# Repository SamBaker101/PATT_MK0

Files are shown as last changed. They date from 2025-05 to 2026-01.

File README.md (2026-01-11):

# PRINT ALL THE THINGS!

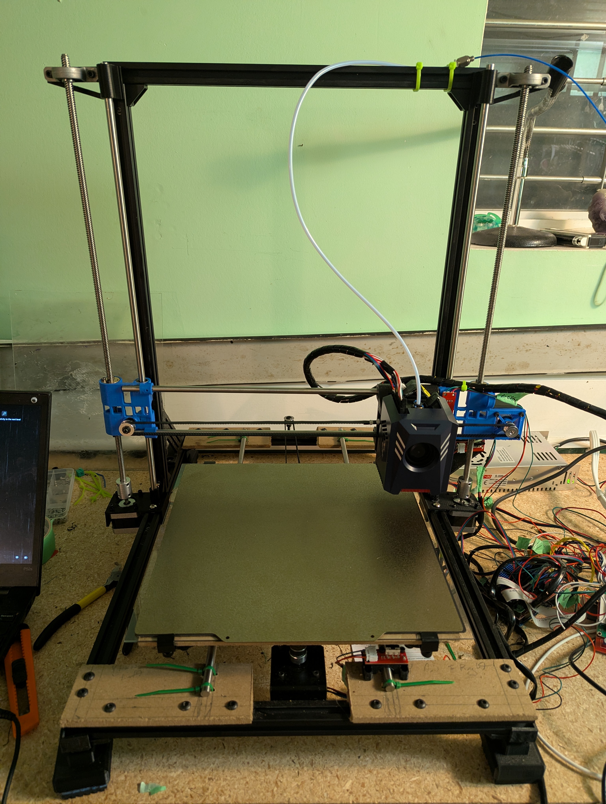
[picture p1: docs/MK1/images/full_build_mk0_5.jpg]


## Overview

A Cartesian, Bed-slinger style, printer. Y motion is applied to the print plate while the hot-end moves in the X and Z directions. This design was selected to give a simple starting point to begin 3d printing. At this point the printer is still a prototype though it does now complete prints reliably. I am working to make incremental improvements to the design over time. More details about my longterm plans can be found in the roadmap below.

- AnyCubic Kobra 2 Direct Drive Extruder Assembly
- Print Area:  290 x 180 x 300 mm (Y will be 250-290 after redesign) 
- Total Size:  480 x 540 x 540 mm
- Arduino Mega - Marlin Firmware
- Reprap 1.4 Control Board
- Orange Pi 4 LTS (Octoprint server)

## Roadmap

The following milestones will be used to direct my efforts in this project. My overall philosophy here has been to begin with the simplest and lowest cost printer possible, regardless of its print speed and quality. Now that the basic device is built I have begun iterating on it to improve its function and reliability.

### MK0 - Zip Ties and Prayers ---- Done!

- Goal: Print a cube
- Status: Complete
- Expected Date: 06/30/2025 
- Completion Date: 07/14/2025
- Comments:  This is meant to be a minimum viable product. The only expectation is that I can connect to it, upload g-code and the printer will make a recognizable attempt to print it. At this time I will not be concerned with the print speed or any issues with the output (within reason). It is also notable that for this step I will not have access to 3d printed parts so many of the brackets and connections will need to be made with a combination of particle board, zip ties and assorted hardware.  
 - [Debrief](https://github.com/SamBaker101/PATT_MK0/blob/main/docs/MK0/MK0_debrief.md)  
 - [Testing](https://github.com/SamBaker101/PATT_MK0/blob/main/docs/MK0/MK0_testing.md)  
 - [BOM](https://github.com/SamBaker101/PATT_MK0/blob/main/docs/MK0/MK0_BOM.csv)     

### MK1 - It Prints Itself?

- Goals: 
     - Replace all temporary parts with self printed parts, these parts must be reliable, consistant and free of major artifacts. 
     - Reorganize electronics onto a board or container integrated into the printer body.
     - Add capability to print remotly over wifi.   
- Status: In Progress
- Expected Date: -
- Comments: Once MK0 is able to complete prints I will begin replacing the temporary plywood parts with custom designed 3d printed parts. I expect this to be an iterative process as replacing selected parts should increase the overall print quality which would in turn allow me to make better versions of those parts. At this time I will also be adding mechanical belt tensioning systems and a reliable bed leveling mechanism. I will also create an electronics board beneath the print bed and clean up the wire routing. Having my laptop wired to print is a major pain point so I will also be adding an OctoPrint server to manage prints.
 - [Debrief](https://github.com/SamBaker101/PATT_MK0/blob/main/docs/MK1/MK1_debrief.md)  
 - [BOM](https://github.com/SamBaker101/PATT_MK0/blob/main/docs/MK1/MK1_BOM.csv)     

## MK2 - Use It

- Goal: 
     - Print a Benchy in under 45min with no major quality issues
- Status: Planned
- Expected Date: Open
- Comments: I think it's important here to use the printer for it's intended purpose for few weeks-months building other projects. I am eager to begin work on some new robotics projetcs and to explore the organizational print community so this shouldn't be a struggle. This will give me a better sense of the printers capabilities and it's pain points.  As I become more familiar with the printer I will iterate on the custom parts and look at other enhancements that can be made to improve performance. 

### MK3 - Upgrade$$$

- Goal: 
     - Print Benchy without major errors in PETG, TPE and ABS. 
     - Print in place chainmail in PLA.
     - Print Benchy in PLA in less than 30 min
- Status: Planned
- Expected Date: Start date + 2 months
- Comments: In my initial build I generally went with the lowest cost option to avoid any expensive mistakes, Now is the time to correct that. Upgrade the control board, motor controllers and hot end to competitive versions. At this time I will also add a heated bed and upgrade any of the PLA printed parts as required. By now I can expect to be well aware of any other issues in the build (linear rods, lead screws ect), so I will take care of any of these issues which I've been putting off.

#### MKZ - Next Steps
- Explore alternate configurations (Core XY, Delta 3d ect.)
- Build a vented, temperature controlled (and sound insulating) cabinet
- Add a second extruder
- Build an AMS
- Build a dry box

## Electrical

| Part | Part Detail | Number | Voltage |Current | Power | Comment |
|---|---|---|---|---|---|---|
|Stepper |Nema 17 | 5 |  24V |1.7A | 40.8W | |
|Motor Controllers |TMC2209 | 4 |  24V |7.5mA | 180mW | Z-Axis can share controller, RAMPS board may need modification to use these  |
|Hot End |Anycubic Kobra2| 1 |24/5V|| 60W | This is temporary but will get me up and running, Power number is a rough estimate as hard numbers are limited  |
|Driver Board |RAMPS1.4 | 1 |  24V || | Interested in designing my own in future, Needed slight modification to run at 24V|
|Main Board |Arduino Mega | 1 |  5V || | Draw 5V off RAMPS board, cut power diode on RAMPS to avoid running 24V in| 
|Limit Switches |Leaf Switches  | 3 | || | |
|Heated Bed |? | 1 | || | Will leave off initial build and upgrade later |
|PSU |LEDMO | 1 | 24V | 20A | 480W | https://www.amazon.ca/gp/product/B08975B78Z/ref=ox_sc_act_title_4?smid=A38O99J0OT8HQ0&th=1  |
|Fans | | 1+ | 12-24V || | |  
|OctoPrint Server |Orange Pi 4 LTS| 1 | 5V || | Has been a bit unreliable so I may switch to an RPi Zero 2W|

### Electronics Box

As part of the MK1 improvements to the original prototype I am currently designing a small sidecar which will house the Arduino Mega (With RAMPS board), The Orange Pi (Being used for Octoprint) and the Reprap Display Board. I am using a sidecar design as the Y-axis design is not yet finalized. In future I may move these electronics under the print bed/y-axis to minimize the printer's footprint.

In order to simplify the wiring I will be organizing the outputs on the back of this box into two D-Sub 25 pin connectors. One of these connectors will have the 18 pin connections for the hotend as well as the 4 pins used to drive the extruder motor. The other contain the other 16 motor connections and the 9 endstop wires. By combining some of the ground and VDD connections I should also be able to allow space for a printed bed in future. I will mismatch these connectors (Male for the printhead and female for the motors) to avoid the possibility of them being plugged in backwards.

The box will also have power inputs for the Orange Pi (USB-C) and the RAMPs board (24V from PSU).

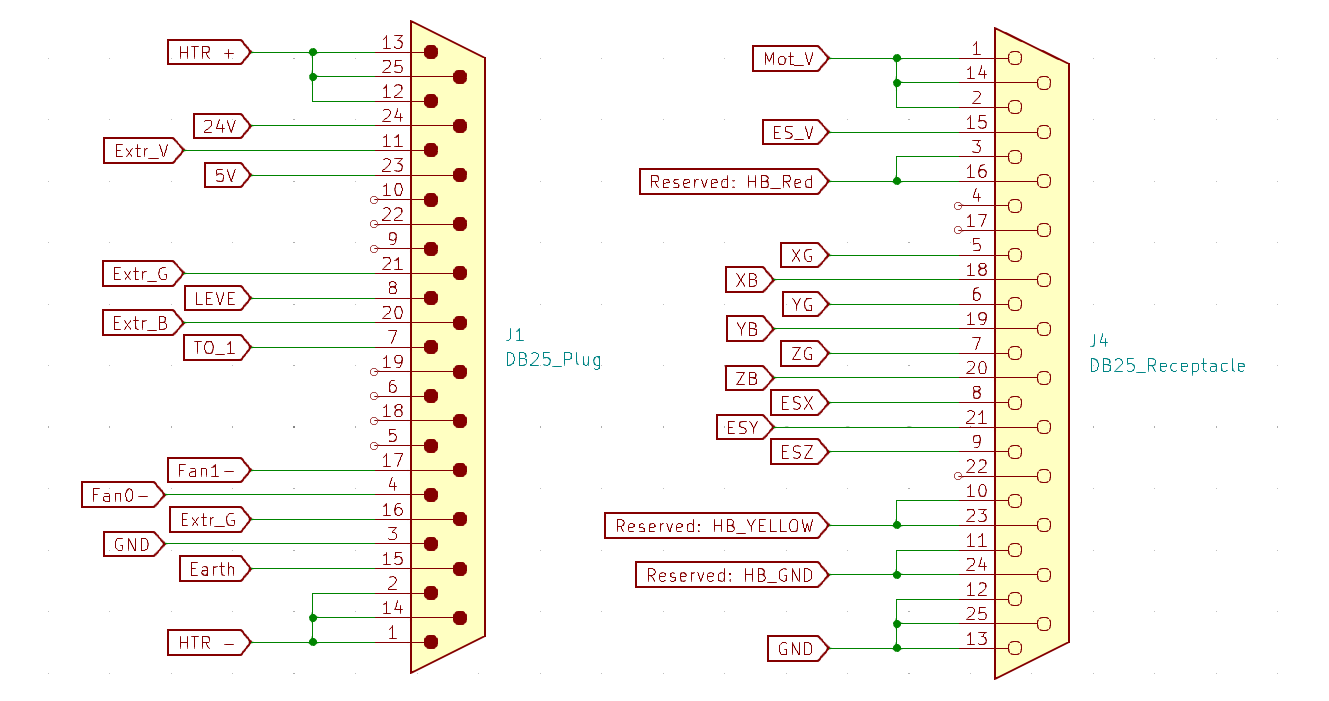
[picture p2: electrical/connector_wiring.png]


## Modelling

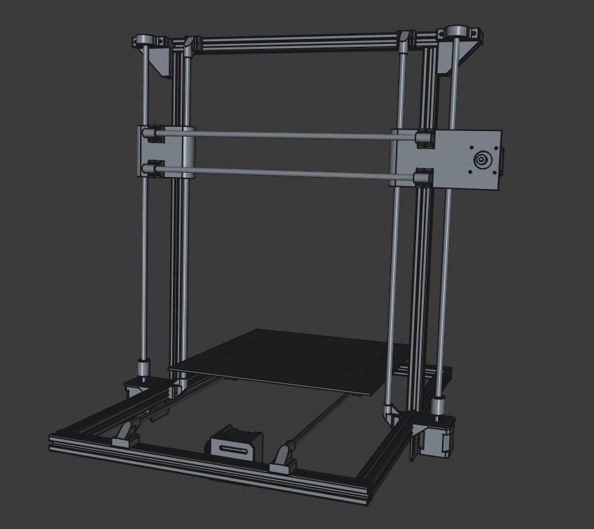
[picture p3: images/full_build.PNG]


NOTE: These models are approximate versions created while developing the printer design. I am in the process of redesigning a number of the parts and will be updating these assemblies as I solidify their new models.

The model is broken into 3 primary sections, one for each axis. The Y-axis assembly includes the print plate while the X-axis includes the hotend and extruder. Each of these main assemblies is further divided into sub assemblies to isolate different segments such as motor drives, frame segments, ect. 

All models were created using FreeCAD 1.0. FreeCAD can be downloaded at the following link.

https://www.freecad.org/

### Models

#### Full Frame

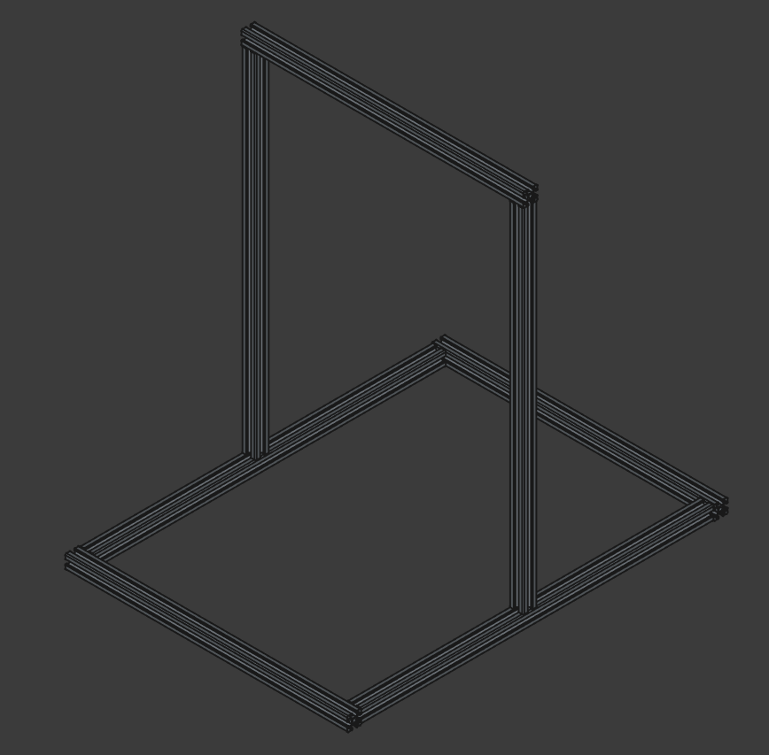
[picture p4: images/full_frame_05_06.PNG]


#### Y-Axis

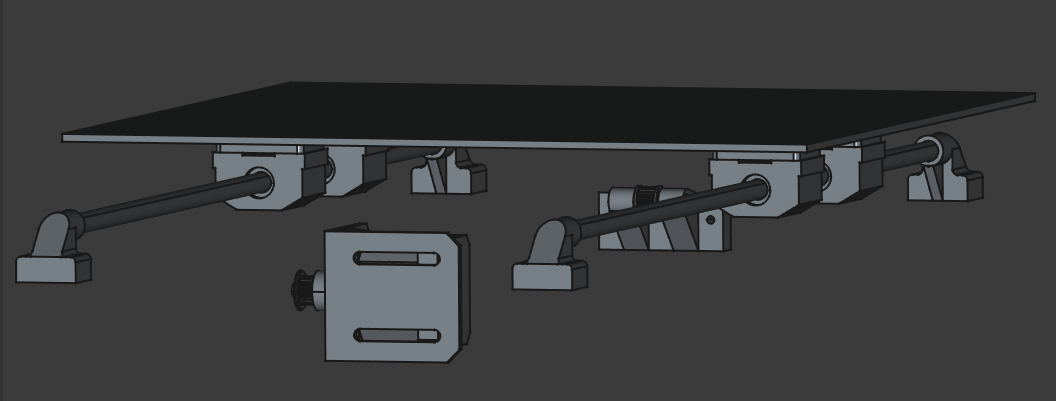
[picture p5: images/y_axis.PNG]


#### X-Axis

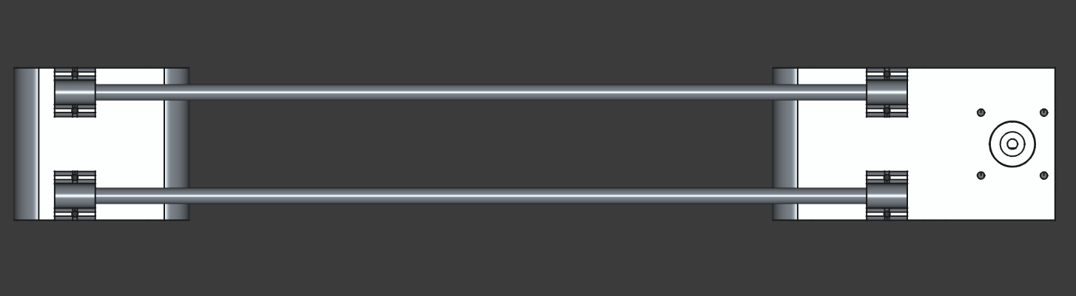
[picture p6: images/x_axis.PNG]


#### Z-Axis

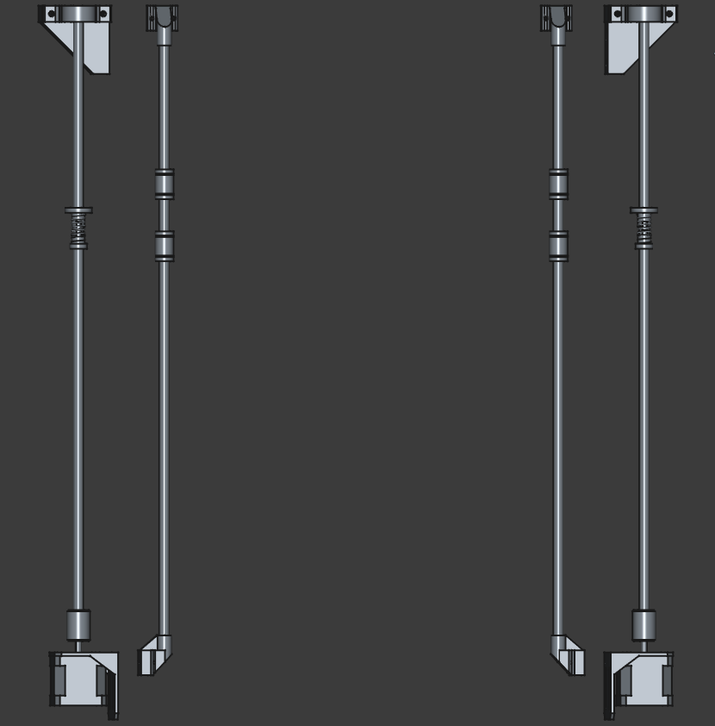
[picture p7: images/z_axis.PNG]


## Parts

My initial approach to part selection was to minimize cost wherever reasonable. My goal was to build a functional printer without a strong focus on print speed or quality. This was to allow time to develop my own skills and identify any knowledge gaps or incorrect assumptions I have.  

Now that I have created a prototype device, I will begin iterating on the device and replacing those lower cost parts with higher end equipment to improve overall quality.

[MK0 BOM](https://github.com/SamBaker101/PATT_MK0/blob/main/docs/MK0/MK0_BOM.csv)

### Custom Parts

Now that MK0 is complete I am beginning the process of replacing the wood panel parts with 3d printed ones. Additionally there are a number of fairly hackey fixes (tensioners, bed leveling, endstops ect) which need more robust solutions.

As I design these new parts I will place the stl files [here](https://github.com/SamBaker101/PATT_MK0/tree/main/models/custom_parts).

Additionally I will include pictures and short descriptions of each part in this [document](https://github.com/SamBaker101/PATT_MK0/blob/main/models/custom_parts/custom_parts.md).

As I get into replacing the more structural components of the build I will also replace the draft assemblies with new more accurate ones.

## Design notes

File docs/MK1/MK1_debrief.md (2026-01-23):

# MK1 - Basic Prototype

Note: MK1 is still in progress. At this point I've redesigned the X and Z axis though further refinement is still necessary.

## Background

The primary goal of MK1 is to move from the somewhat hacked together MK0 to a more robust and coherent platform that I can build on for future developements. This primarily involves replacing the wood panel parts with 3d printed ones. The majority of the zip ties should also be removed during this step. In adition I have added an Orange Pi to run an OctoPrint server. Finally I will be making some refinements to the wiring and electrical system. 

## Build Overview

### New Part Designs
### Octoprint Server

## Configurations

## Lessons

## Next Steps

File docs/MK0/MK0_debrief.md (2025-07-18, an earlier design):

# MK0 - Basic Prototype

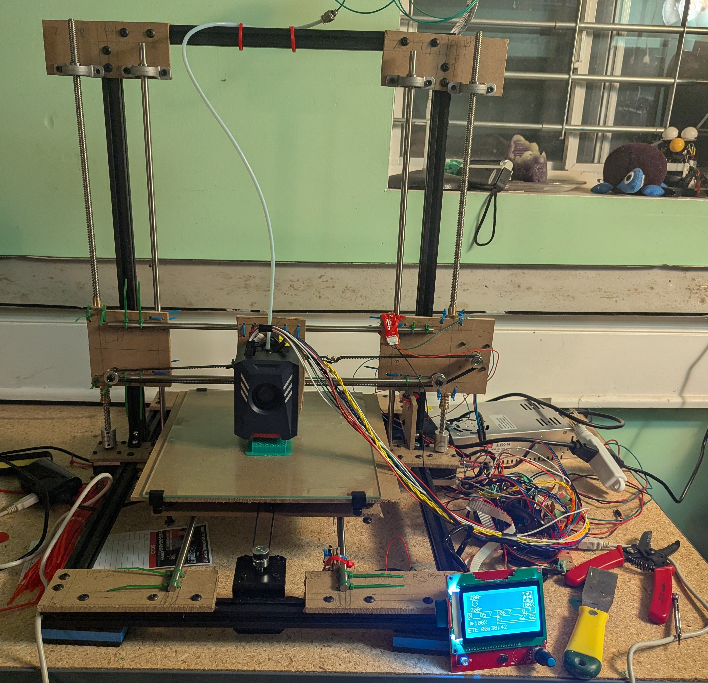
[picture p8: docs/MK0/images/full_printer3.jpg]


## Background

It's not pretty... but it works

The primary constraint with this prototype was one many people run into when building their first 3d printer. That is, that I didn't have a 3d printer. Since I couldn't easily prototype or manufacture custom parts I limitted myself to using only parts I could make using basic tools. These tools included a jig-saw, a power drill, a soldering iron and a variety of hand tools. 

I opted to start with a large build area. My initial plan was to have a full 300mm cubic build space though unfortunately for this initial prototype I ended up having to limit that to 175mm x 175mm x 250mm (more on that later). This may have been for the best as bed leveling proved challenging on this initial build.

While it's my intention to create my own printhead for this project I initially used a direct drive head from an Anycubic Kobra 2. I selected this for it's low cost and the fact that it was complete and self contained. A word of caution is that Anycubic does not open source their hardware or software so I did have to do some reverse engineering to get it working. I will not be publishing the details of that reverse engineering to avoid posting any copywritten IP.

The printer is based on the REPRAP 1.4 control board using an Arduino MEGA board. It operates using Marlin firmware.

## Build Overview

The main frame is built using a combination of aluminum extrusion and composite wood paneling that has been cut to sizes/shape and drilled as required. It is held together with a combination of metric hardware and zip-ties.

As discussed prior I am using an Anycubic printhead which moves in X on a belt driven carriage. The X-axis then moves vertically (Z) on a pair of lead screws.

The bed is a pane of glass which slides in the Y direction (Forward and Back) on a belt drive. This glass pane is supported by 4 bolts which can be adjusted to level the print bed.

Currently the electrical components (REPRAP board and power supply) are stored on the table beside the printer.

## Configurations

Full config details can be found in the Marlin configuration document here:  
[Configuration.h](https://github.com/SamBaker101/PATT_MK0/blob/main/software/Marlin-2.1.2.5/Marlin/Configuration.h)  

All stepper motors are set up to use 1/16 microstepping.

As mentioned above I have restricted the printer to use a 175x175x250mm build space. At time of writing I have not yet tested larger prints but will be doing so shortly.

In my initial testing I had the Z axis bind when using too high of a feedrate. For this reason I have significantly limited the speed of the printer. I have not tested the limits for these metrics as yet but will begin increasing them slowly as I begin building the parts for MK1.  

## Lessons
While perfection was never the goal here this project was not without it's problems. Below I would like to detail some of the main issues I encountered building this prototype and discuss the lessons learned from them. 

### Bed Size and Verticle Rods
As mentioned earlier I had to reduce the bed size from my projected 300mm cubed to 175x175. This was due to the geometry of the x and y axis. 

For the X-axis I opted to have the verticle rods sit inside the frame. This choice was made to simplify the brackets used to hold these rods. Additionally since I was using composite panels I ended up having to make the X carriage and brackets larger than expected which blocks some of the X travel.

The Y-axis has similar issues with the size of it's brackets but also could be corrected by placing the bearings closer together so that the bed could hang over these brackets further. This is a double edged fix though as it could impact the stability of the bed.

This is also the reason I am using a plain glass panel as a print surface. I purchased a removable build plate which I will be using for future iterations but it does not fit on the current build.

### Z-Endstop Relocation
In my initial design I had the Z-Endstop at the top of the axis. When testing I found it was very difficult to get a consisting starting position on prints. To mitigate this I moved the endstop to the bottom.

The major difference here is that when the endstop is at the top you can configure the starting position via software, telling the axis how far to move from it's home position. Now the endstop would need to be physically moved to adjust the height from the build plate. 

This may be less of an issue in future builds where the frame and axis have less slop. In all likelyhood though, I will eventually switch to a bed probe of some kind. That means I am not too concerned about this change going forward. 

### Bed Leveling Issues
My bed leveling mechanism consists of 2 panels. The lower panel holds the bearings and has a bolt in each corner. These four bolts are placed from below facing up with a nut placed loosely on each. tightening or loosening the nut adjusts how much of the bolt stands above the plate while the remainder of the bolt hangs below.

The upper panel holds the glass buildplate. Glued to the bottom of the upper plate are 4 spacers which sit overtop of the bolts.  

This system works but can be frustrating to use for the following reasons. 
- There is quite a bit of slop between the two plates
- 4 Adjustment points are being used when only 3 are required
- Bolt must be held while nut is turned
- Nuts/Bolts can be very hard to reach

I will be redesigning this system to make it simpler and easier to use in future iterations. This will include adding wheels to help turn the nuts (and/or bolts) and adding tension springs below the lower plate to keep the bolts stabalized.

### Wood Panelling is not Nice
Because I am the way I am, I went to the hardware store and bought the cheapest "wood" I could find to create the brackets. This came in the form of a composite panelling which appears to be some kind of compacted cardboard product... 

While functional it is deeply unpleasant to work with. It flakes away in layers when being drilled or cut and produces huge amounts of dust and shavings. if I was doing this again I would definitely spend a few extra dollars for a better material.

Luckily these panels were always meant to be temporary. As I redesign the printer for MK1 I will be removing these parts and replacing them with printed ones.

### Hotend Sag
Because I used a direct drive extruder the hotend is fairly heavy. This combined with the makeshift X carriage causes the printhead to sag. This means the hotend is not perpendicular to the build plate. 

The problem is not significant enough to cause prints to fail but definitely influences the quality. For the next iteration I will be creating a new X carriage and printhead bracket so this issue will be corrected at that point.

## Next Steps

- Replace The Panelling and Zip Ties
- Add Feet and Additional Braces to Frame
- Straighten Belt Runs and Add Tensioners
- Create Room for Full Sized Bed
- Create Better Bed Leveling System
- Remodel Print Head Carriage
- UART for Motor Controllers
- Increase Print Speeds
- Add Electrical Board and Fix Wire Routing

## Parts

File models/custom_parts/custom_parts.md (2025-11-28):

# Custom Parts

## Print Bed
### Bed Leveling Wheel
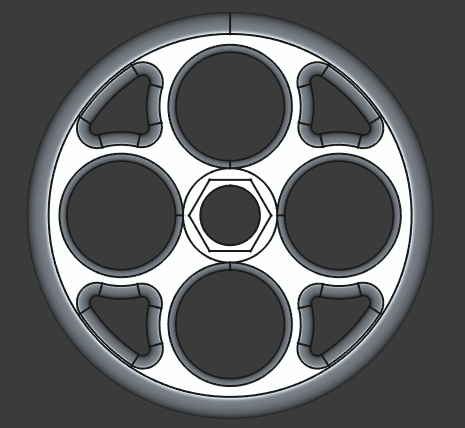
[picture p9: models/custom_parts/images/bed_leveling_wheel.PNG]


Simple wheel to sit over bed levelling nuts and make adjustment easier. This is a quick mock-up which I may return to later to refine.

### Adjustment Bolt Sleeves
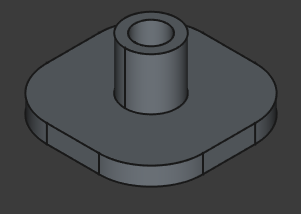
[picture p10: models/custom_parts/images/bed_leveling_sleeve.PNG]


The spacers I used in the initial build have too large an internal diameter so there is slop in the bed, especially if the level screws are set too high. Additionally they are simple cylinders so the glue joints break easily. This part is meant to correct these issues.

### Spool Holder
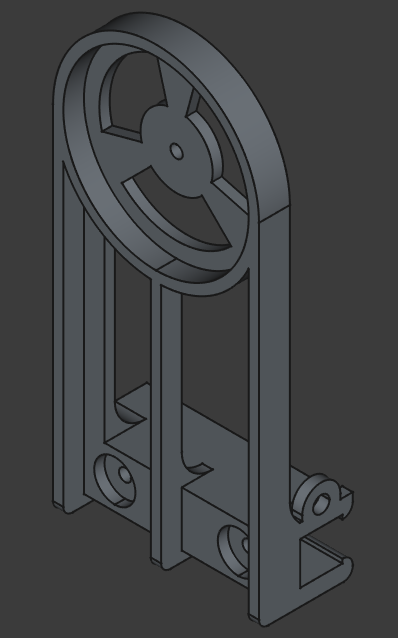
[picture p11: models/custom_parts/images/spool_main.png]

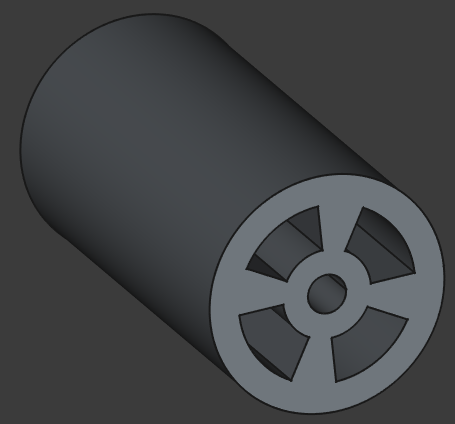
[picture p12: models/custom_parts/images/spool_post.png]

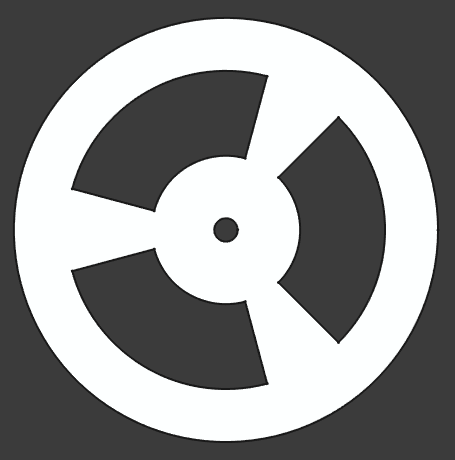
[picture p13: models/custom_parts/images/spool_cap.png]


Spool holder for the top of the printer. I had to go back and add some ribs to strengthen this print. If it is still to week I may try a carriage style design where the post is reenforced on both sides.

### Lower Bed Carrier
### Bed Carrier

## Structural
### Feet
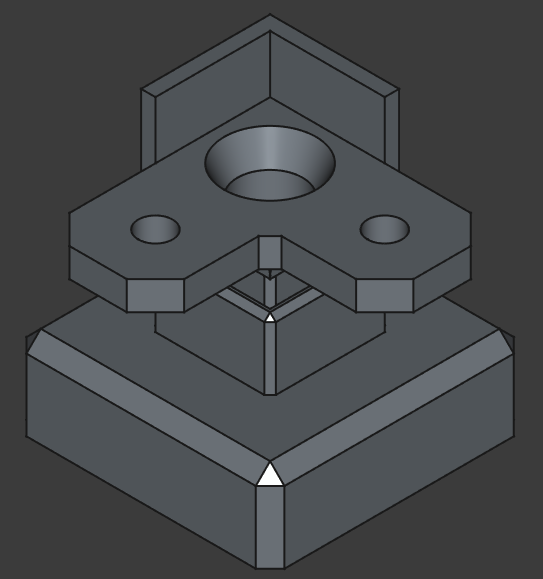
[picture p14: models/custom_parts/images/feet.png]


It's a foot! This is meant to stabalize the frame as well as raise the printer to allow room for the electronics board. Comprised of two seperate pieces (Bracket and Base). Rubber blocks will be attached to the base.

One change that I will make in my next iteration of this part ill be to extend the tabs which bolt to the frame. The screw holes on these tabs currently overlap with the lower portion of the foot making tightening the screws challenging.

### Corner Re-enforcements
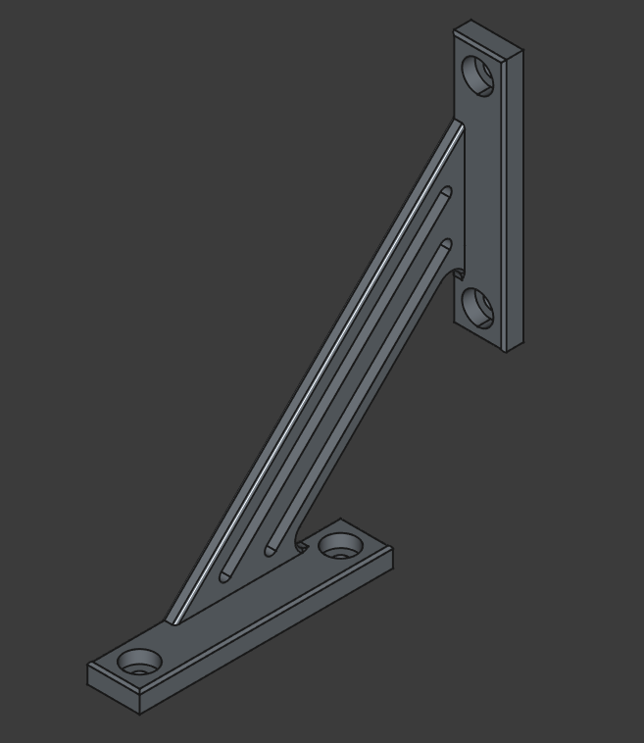
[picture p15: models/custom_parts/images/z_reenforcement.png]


This is a simple bracket to stabalize the connection between the z axis frame and the lower (y-axis) frame.

## Brackets and Carriages
### Y-Axis Brackets (Front and Back)
### Z-Axis Brackets (Top and Bottom)

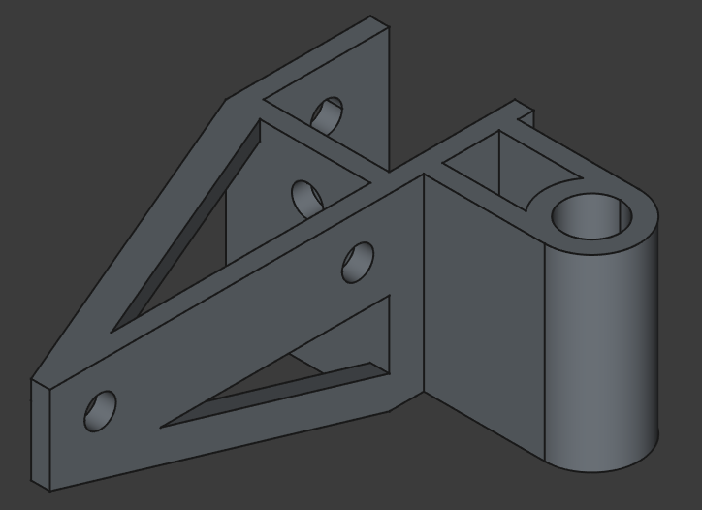
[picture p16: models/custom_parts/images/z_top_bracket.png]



Lower bracket is not strong enough. Also center motor hole is two small. Second revision being tested.

### Z Carriages (Left and Right)




These carriages are working fairly well. They could use some reenforcement though I did print them with limitted infill/resolution so reprinting may help.

End stop holder should be moved up slightly to give clearance for timing belt. More space should be opened between threaded z-rod attachments to simplify installation.

More space is needed for x axis to pass through body, I had to drill/melt to make space.

### X Carriage



Insufficient space for extruder motor so I've had to use a spacer, support flaps interfering with timing belt need to be repositioned (I snapped them off for now).

## Electrical Components
### End Stop Holders


This is a bracket to hold the limit switches. The bracket is designed to allow for minor adjustment of the switch position. This initial version of the bracket is made to work with the current wood panel frame brackets and will need to be revisited as I refine the rest of the frame design. The Z-Axis will require an additional bracket to hold the limit switch out from the frame in the correct position.

### Z Endstop Holder


This holder works in conjunction with the general endstop holder to hold the z limit switch away from the frame. The slots alow fine tuning of the z height.

### Electrical Component Board
### Cable Management Aids

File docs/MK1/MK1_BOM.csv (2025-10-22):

Num | Quantity | Part | Description | Link
0 | 1 | Glass Pane | 12 x 12 | I took this from a thrift store picture frame
1 | 4 | Linear Bearing | Bearing
2 | 2 | Belt Clamp | Part of timing belt kit
3 | 2 | Timing Belt | Part of timing belt kit
4 | 2 | Timing Belt Idler | Part of timing belt kit
5 | 1 | Timing Belt Gear | Part of timing belt kit
6 | 2 | Linear Rod 400mm | 8mm diameter rod
7 | 4 | Linear Rod 500mm | 8mm diameter rod
8 | 3 | 2020 T extusion 400mm | 2020 T extrusion
9 | 4 | 2020 T extusion 500mm | 2020 T extrusion
10 | 10 | 2020 L-Bracket | 2020 Extrusion compliant L-bracket
11 | 4 | Stepper Motor | Nema 17
12 | 1 | Stepper Bracket | L Bracket for Nema 17 stepper motor
13 | 1 | Power Supply | 24V 5A power supply
14 | 1 | Controller | Arduino Mega 2560
15 | 1 | RAMPS1.4 Board | RAMPS1.4 board
16 | 4 | Stepper Motor Driver | TM2209 stepper motor driver
17 | 1 | LCD Display | 12864 LCD display
18 | 1 | DC-DC converter | 24V -> 5V cpnverter for Arduino and LCD
19 | 1 | Safety Plug | Fused wall outlet plug
20 | 3 | Endstop Switch | Mechanical endstop switch
21 | 1 | Hotend Assembly | AnyCubic Kobra2 Direct Feed Hotend Assembly
23 | 1 | Print Surface | 290x290mm PEI print surface
25 | 2 | Lead Screw | 8mm diameter 8mm lead
26 | 2 | Lead Screw Nut | 8mm lead screw nut
27 | 4 | 8mm Lead Screw Bearing | Came with lead screw
28 | 2 | 8mmx5mm Lead Screw Coupler | Coupler for lead screw
29 | 50 | M5 T-Nut | 2020 extrusion compliant T-nut
30 | 18 | M5x8mm Button Head Screw | Standard Metric screw
31 | 30 | M5x12mm Button Head Screw | Standard Metric screw
32 | 2 | M5x16mm Button Head Screw | Standard Metric screw
33 | 4 | M8x35mm Button Head Screw | Standard Metric screw
34 | 4 | M8x22mm Spacer | Plastic spacer for M8 screw
35 | 4 | M8 Hex Nut | Standard Metric nut
36 | 8 | M3x6mm Hex Head Screws | Standard Metric screw
37 | 8 | M4x6mm Hex Head Screws | Standard Metric screw
38 | 1 | PLA | 1KG Spool
39 | 1 | Orange Pi 4 LTS

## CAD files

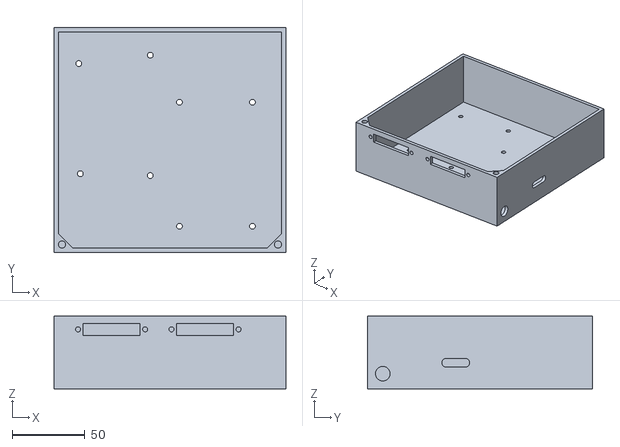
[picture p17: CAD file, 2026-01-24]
models/custom_parts/electrical/electronics_box_main.stl
159.0 x 154.2 x 50.0

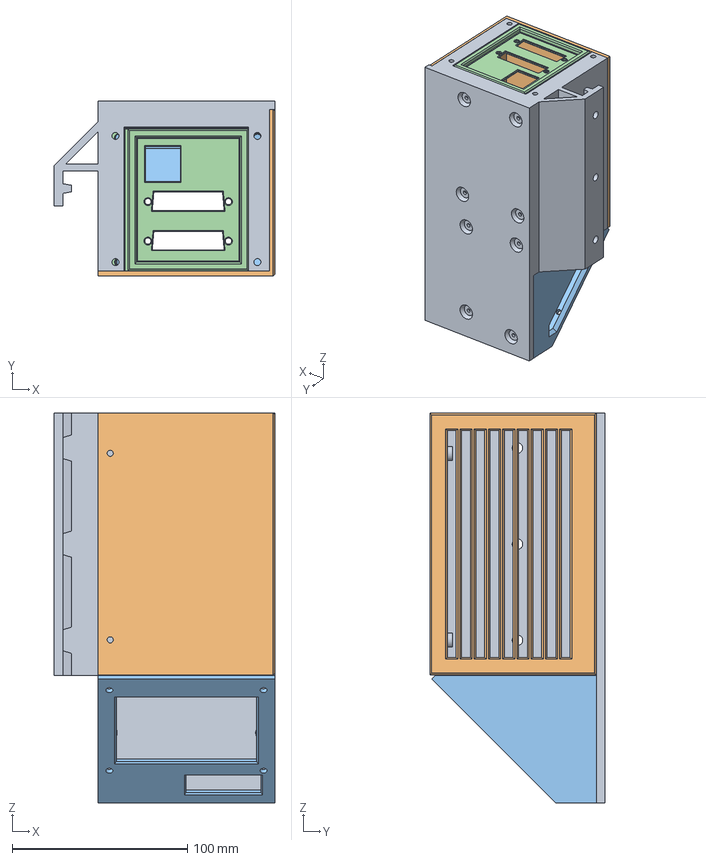
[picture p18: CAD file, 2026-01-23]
models/main_assemblies/electronics_box_assembly.FCStd
126.1 x 100.0 x 222.6 mm
electronics_box_main_001
electronics_box_top_001
electronics_box_front_001
electronics_box_back_panel_001

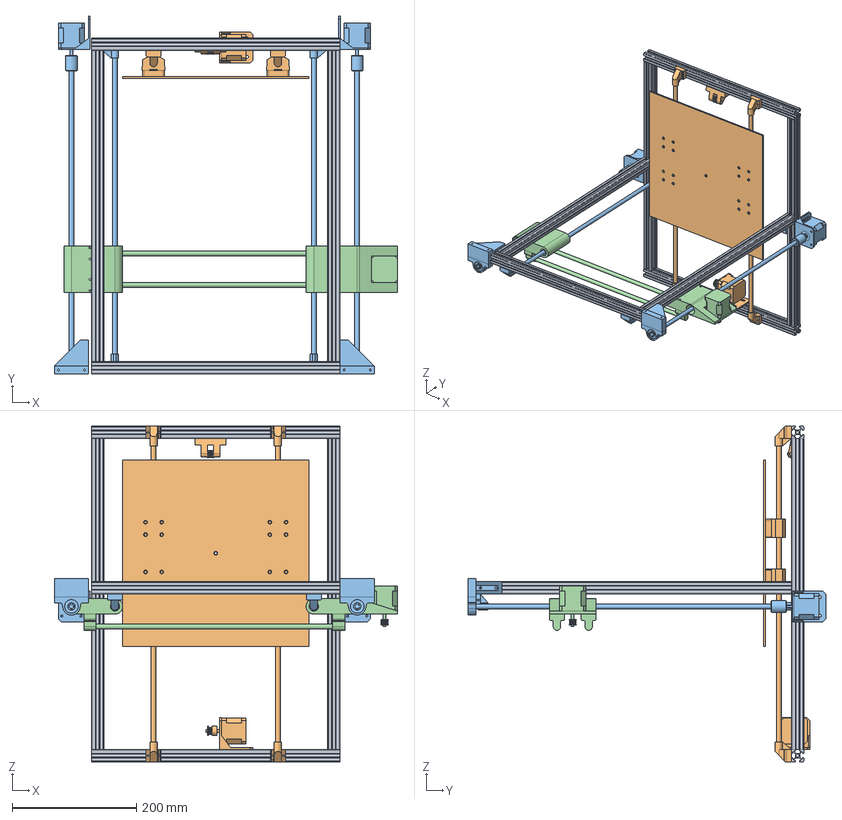
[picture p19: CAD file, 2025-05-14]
models/main_assemblies/full_build.FCStd
552.1 x 575.8 x 540.0 mm
full_frame_001
y_axis_assembly_001
z_axis_assembly_001
x_axis_assembly_001

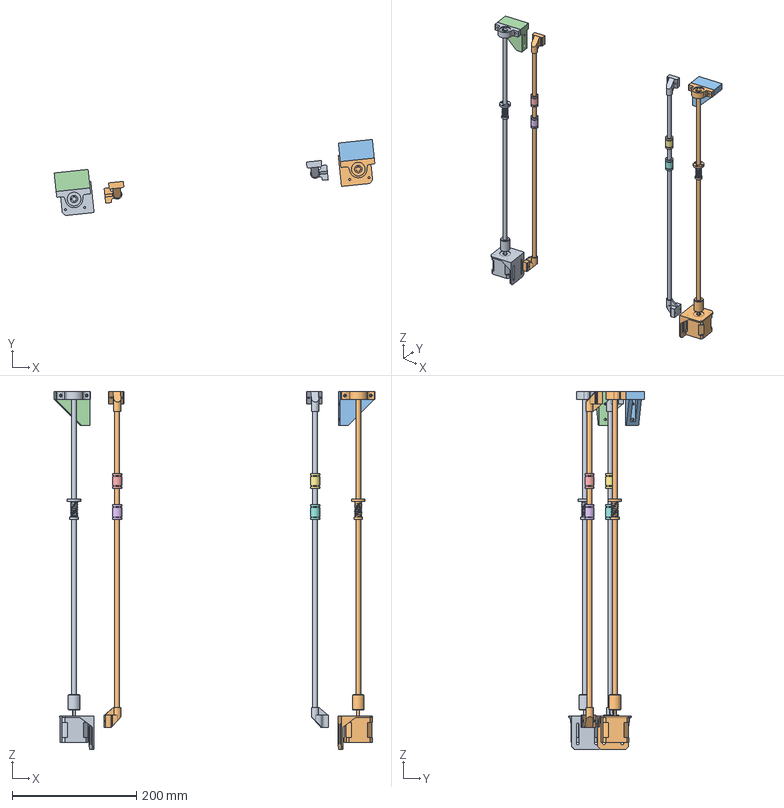
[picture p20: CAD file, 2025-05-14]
models/main_assemblies/z_axis_assembly.FCStd
515.8 x 122.3 x 575.8 mm
y_axis_rod_90_001
y_axis_rod_001
14_lead_screw_top_bracket_001
14_lead_screw_top_bracket_002
1_2_linear_bearing_simple_001
1_2_linear_bearing_simple_002
1_2_linear_bearing_simple_003
1_2_linear_bearing_simple_004
z_axis_drive_right_001
z_axis_drive_left_001

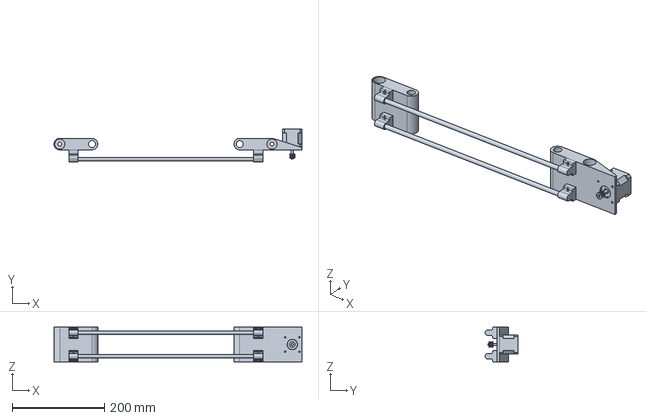
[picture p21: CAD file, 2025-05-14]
models/main_assemblies/x_axis_assembly.FCStd
536.8 x 71.0 x 75.0 mm

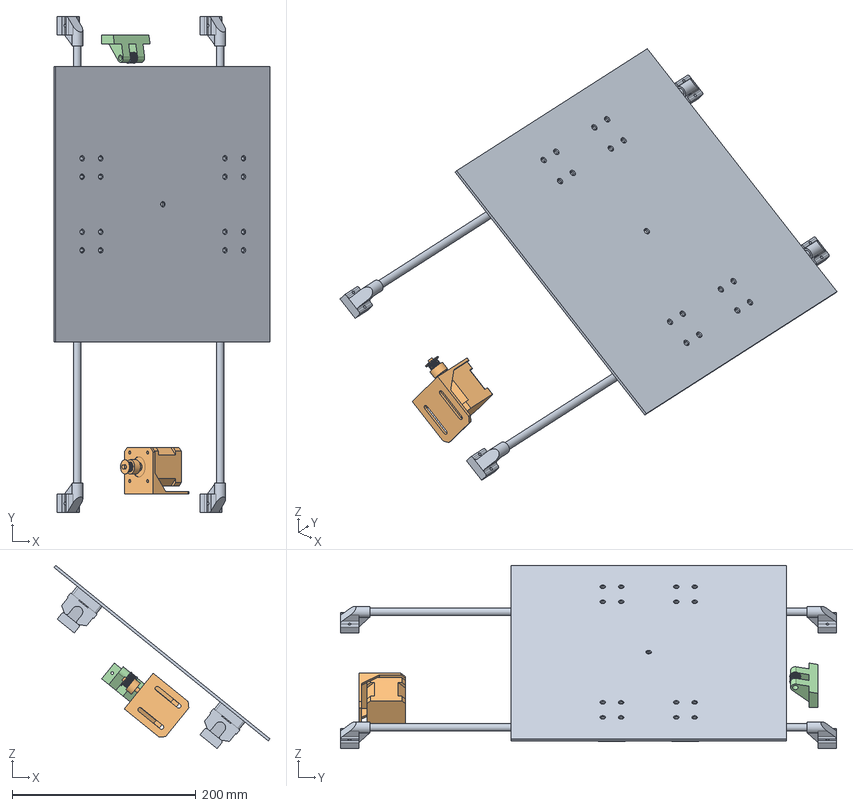
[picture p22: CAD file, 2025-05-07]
models/main_assemblies/y_axis_assembly.FCStd
235.1 x 540.0 x 199.4 mm
y_axis_rod_and_plate_001
y_axis_motor_001
8_timing_idler_001
8_1_timing_idler_bracket_001

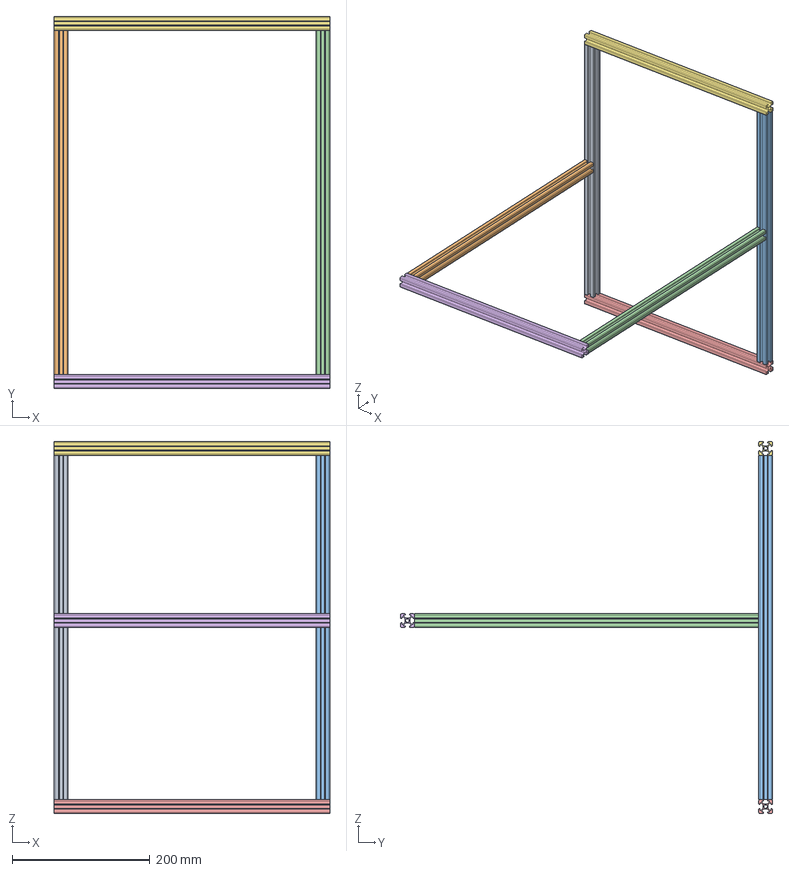
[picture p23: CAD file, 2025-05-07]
models/main_assemblies/full_frame.FCStd
400.0 x 540.0 x 540.0 mm
5_3_2020_t_extrusion_500mm_001
5_3_2020_t_extrusion_500mm_002
5_3_2020_t_extrusion_500mm_003
5_3_2020_t_extrusion_500mm_004
5_2_2020_t_extrusion_400mm_001
5_2_2020_t_extrusion_400mm_002
5_2_2020_t_extrusion_400mm_003

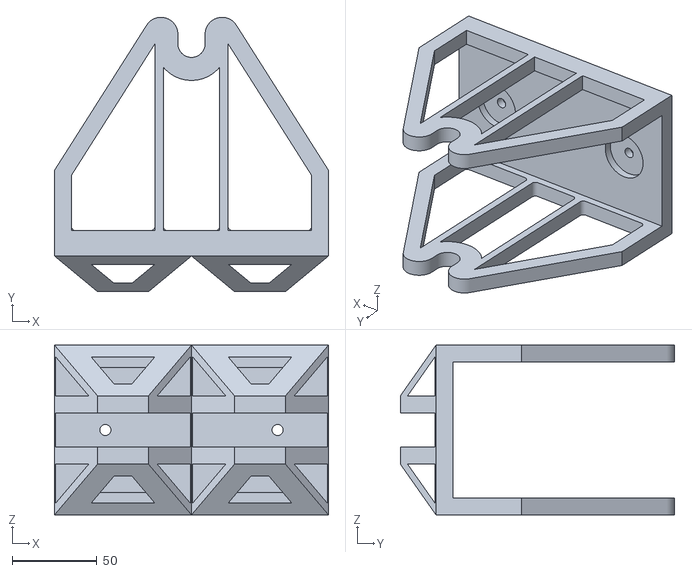
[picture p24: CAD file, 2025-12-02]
models/custom_parts/frame/spool_holder_main.stl
161.4 x 161.6 x 100.0

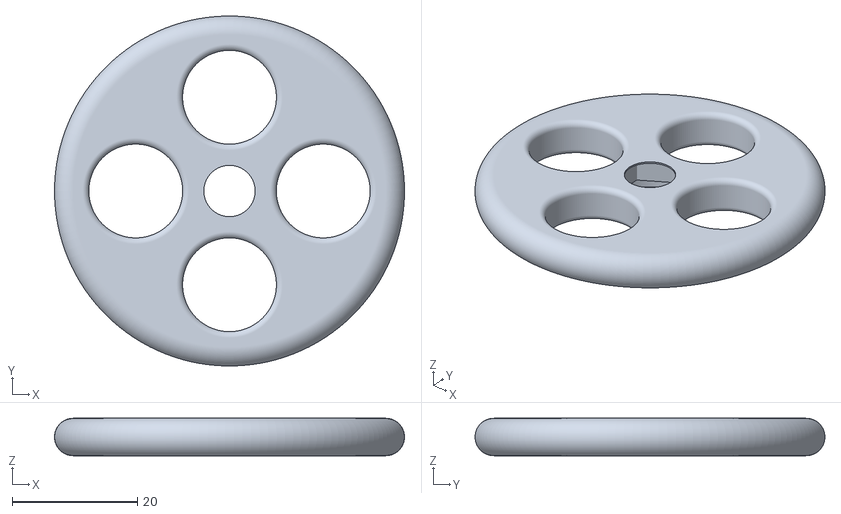
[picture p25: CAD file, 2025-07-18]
models/custom_parts/bed_leveling_wheel.stl
56.0 x 56.0 x 6.00

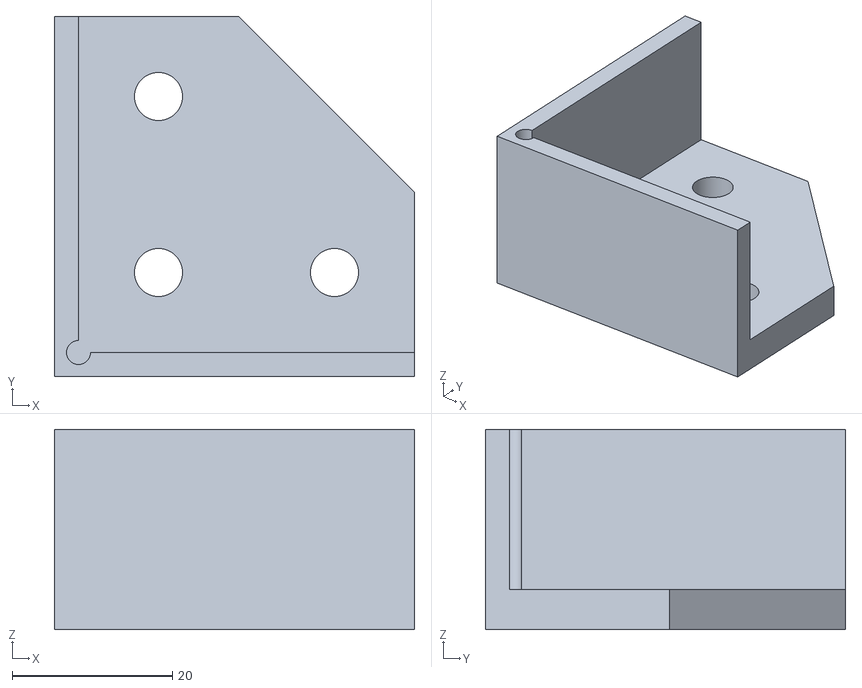
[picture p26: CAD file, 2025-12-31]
models/custom_parts/frame/corner_bracket.stl
45.0 x 45.0 x 25.0

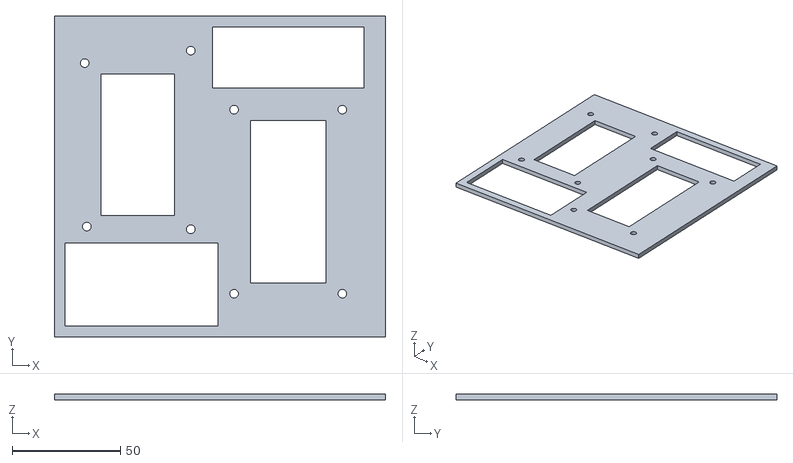
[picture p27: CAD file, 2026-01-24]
models/custom_parts/test_plates/test_plate_arduino_mega2.stl
153.0 x 148.2 x 3.00

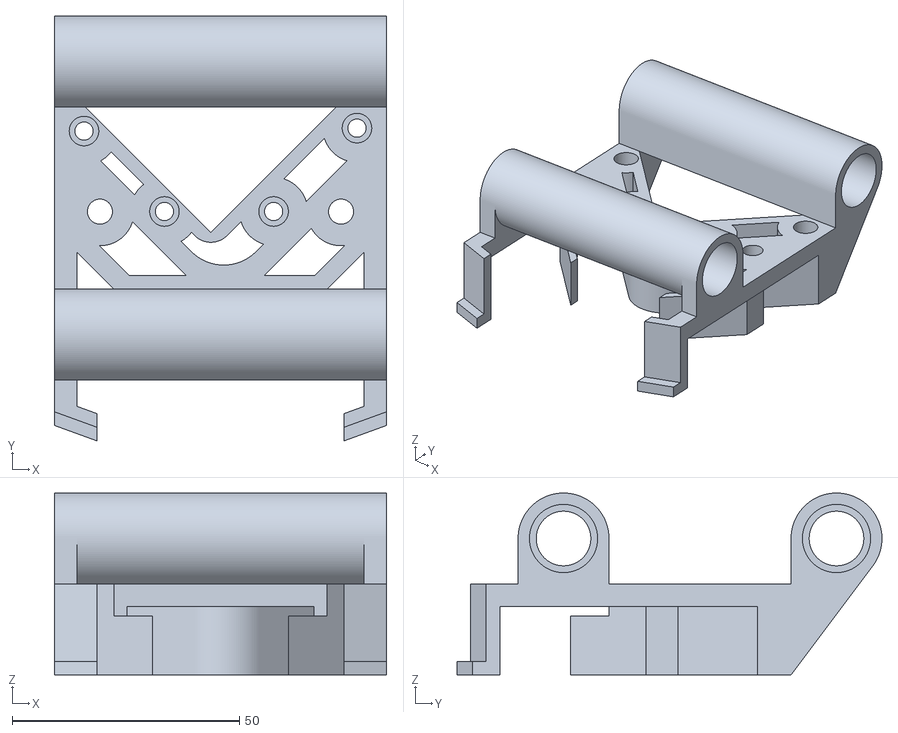
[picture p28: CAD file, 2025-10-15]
models/custom_parts/x_axis/x_carriage.stl
73.0 x 93.4 x 40.0

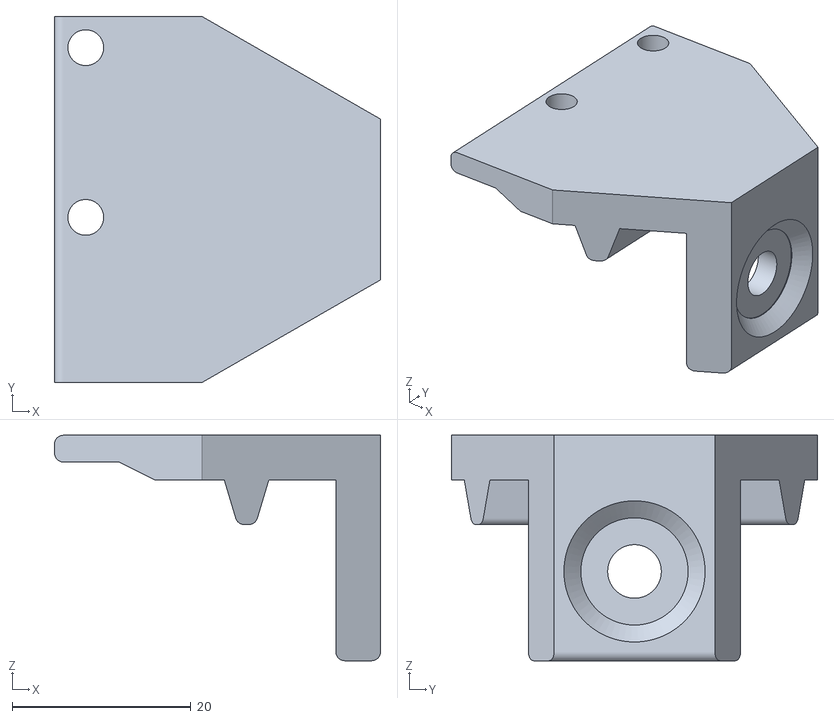
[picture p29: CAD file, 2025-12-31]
models/custom_parts/y_axis/y_axis_endstop_holder.stl
36.5 x 41.0 x 25.3

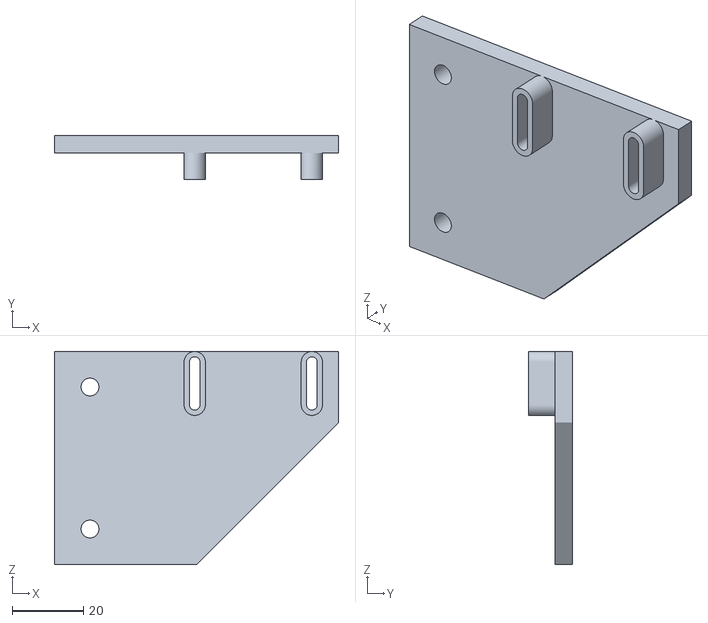
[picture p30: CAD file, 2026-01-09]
models/custom_parts/z_axis/z_endstop_bracket.stl
80.0 x 12.5 x 60.0

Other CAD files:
models/parts/4_rod_end_caps.FCStd
models/sub_assemblies/y_axis_rod.FCStd
models/tests/axis_test_arrow.FCStd
software/cura_project/cura_slicer_settings.3mf
models/custom_parts/electrical/electronics_box_back_panel.stl
models/custom_parts/electrical/electronics_box_front.stl
models/custom_parts/electrical/electronics_box_top.stl
models/custom_parts/electrical/wire_clamp.stl
models/custom_parts/electrical/wire_clamp_top.stl
models/custom_parts/frame/feet.stl
models/custom_parts/frame/feet2.stl
models/custom_parts/frame/foot_base.stl
models/custom_parts/frame/foot_bracket.stl
models/custom_parts/frame/foot_post.stl
models/custom_parts/frame/spool_holder_base.stl
models/custom_parts/frame/spool_holder_clip.stl
models/custom_parts/frame/spool_holder_clip_narrow.stl
models/custom_parts/frame/spool_holder_post.stl
models/custom_parts/frame/spool_holder_post_narrow.stl
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

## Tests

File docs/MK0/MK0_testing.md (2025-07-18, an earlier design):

# MK0 Testing and Adjustments

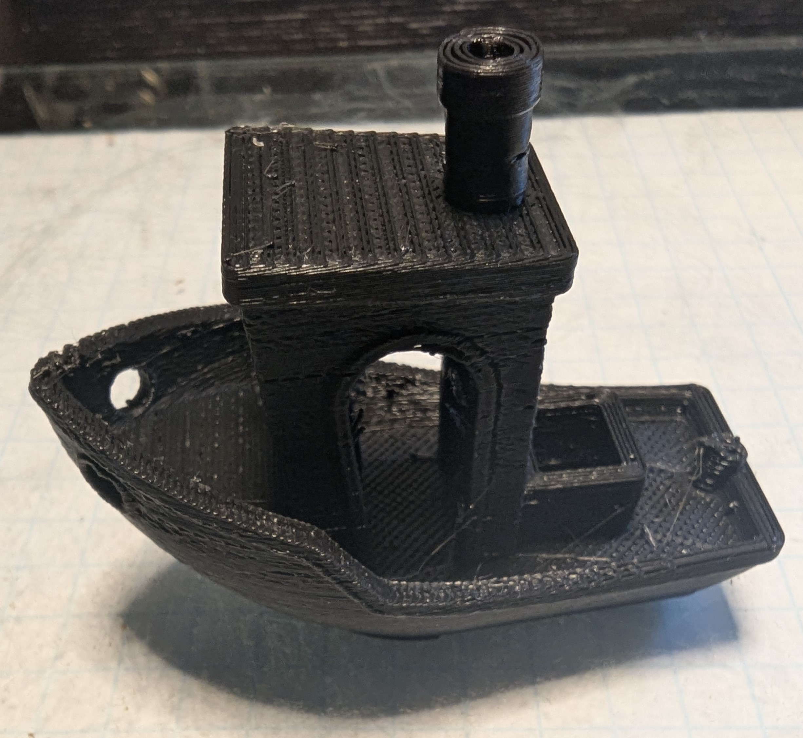
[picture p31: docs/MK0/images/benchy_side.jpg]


## 10mm Cube Testing
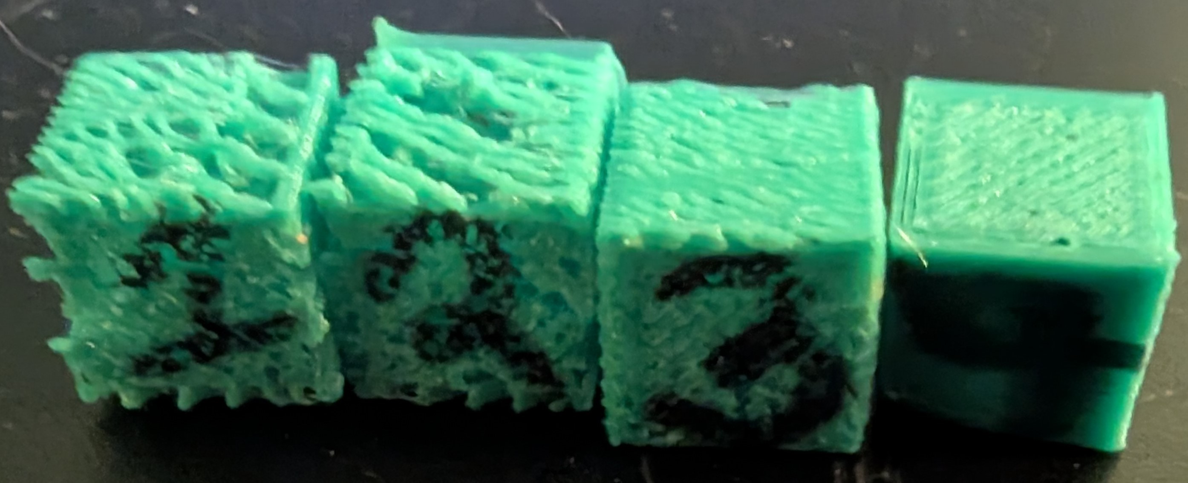
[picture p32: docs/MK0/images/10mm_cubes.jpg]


Quick sanity checks with 10mm cubes, identified and fixed issues with underextrusion

## 40mm Cube
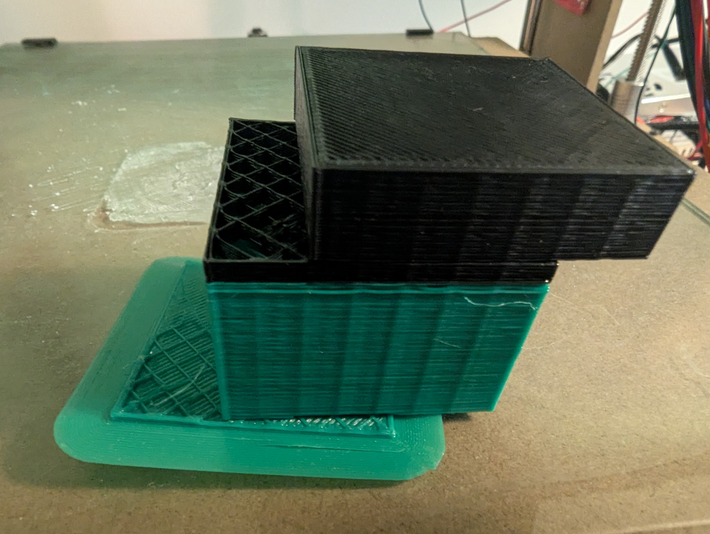
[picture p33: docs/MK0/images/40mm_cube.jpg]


Attempting a larger build, Had Serious layer adhesion issues. This was caused by me setting the layer height to high.



View through the top shows how sparse top layer is. I didn't identify the root cause of this until after my first Benchy but it turns out my slicer had the filiment size set incorrectly.

## Benchy

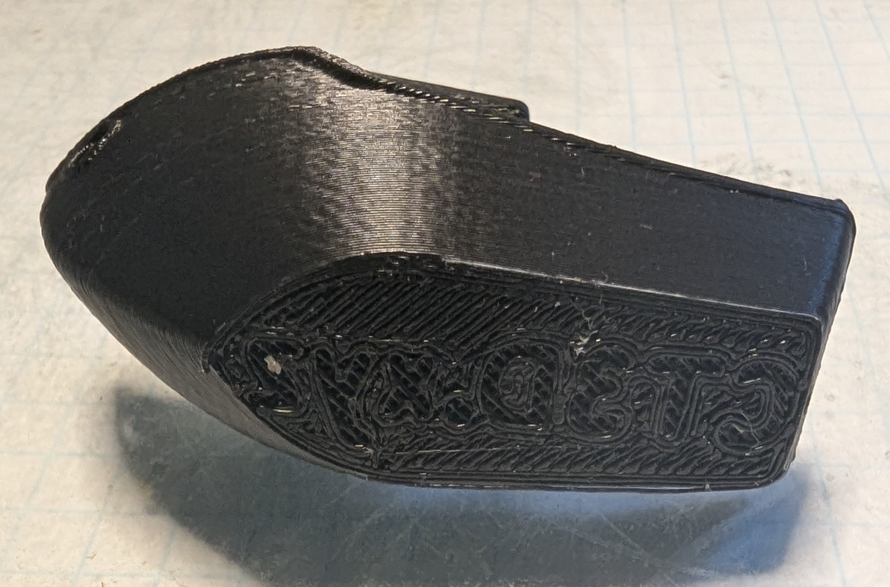
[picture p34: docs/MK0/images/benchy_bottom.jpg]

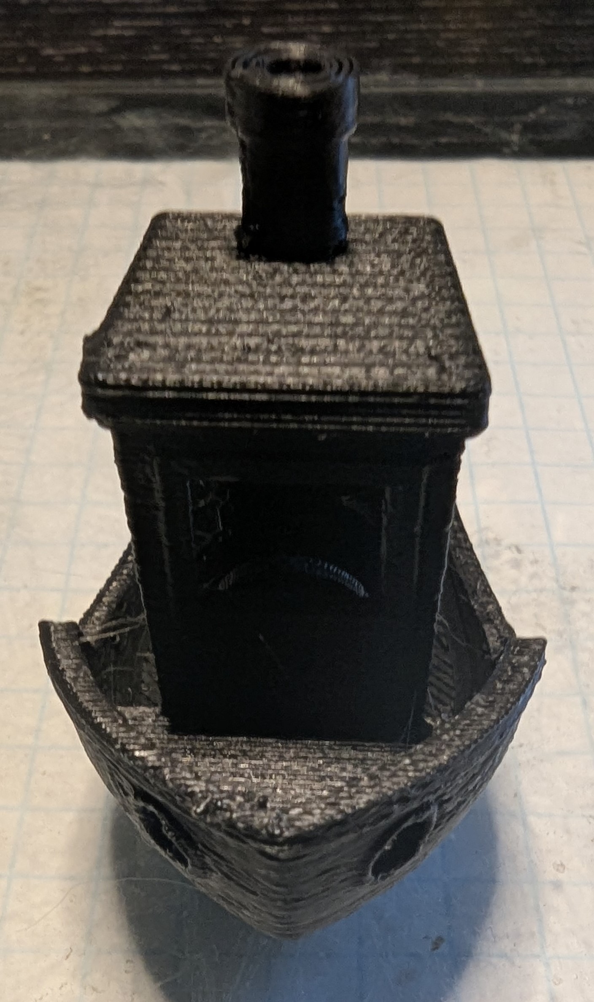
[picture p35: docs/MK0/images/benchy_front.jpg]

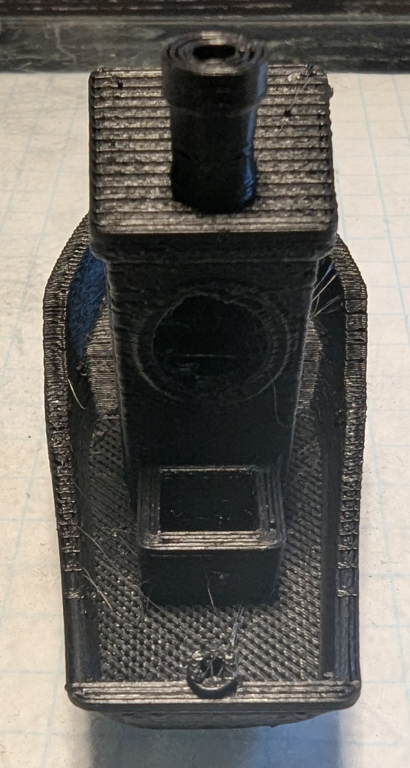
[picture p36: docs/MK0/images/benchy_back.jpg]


Its a Benchy! This was while my filiment size was still incorrect which caused some issues. My results were greatly improved when I fixed that problem.

Still experiencing some extraction issues and artifacting.

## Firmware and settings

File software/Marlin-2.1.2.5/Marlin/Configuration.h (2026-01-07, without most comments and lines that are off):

#pragma once
#define CONFIGURATION_H_VERSION 02010205
#define STRING_CONFIG_H_AUTHOR "(none, default config)"
#define SHOW_BOOTSCREEN
  #define MOTHERBOARD BOARD_RAMPS_14_EFF
#define SERIAL_PORT 0
#define BAUDRATE 250000
#define CUSTOM_MACHINE_NAME "PATT-MK0"
#define X_DRIVER_TYPE  TMC2209
#define Y_DRIVER_TYPE  TMC2209
#define Z_DRIVER_TYPE  TMC2209
#define E0_DRIVER_TYPE TMC2209
#define EXTRUDERS 1
#define DEFAULT_NOMINAL_FILAMENT_DIA 1.75
#define TEMP_SENSOR_0 5
#define TEMP_SENSOR_1 0
#define TEMP_SENSOR_2 0
#define TEMP_SENSOR_3 0
#define TEMP_SENSOR_4 0
#define TEMP_SENSOR_5 0
#define TEMP_SENSOR_6 0
#define TEMP_SENSOR_7 0
#define TEMP_SENSOR_BED 0
#define TEMP_SENSOR_PROBE 0
#define TEMP_SENSOR_CHAMBER 0
#define TEMP_SENSOR_COOLER 0
#define TEMP_SENSOR_BOARD 0
#define TEMP_SENSOR_REDUNDANT 0
#define DUMMY_THERMISTOR_998_VALUE  25
#define DUMMY_THERMISTOR_999_VALUE 100
#if TEMP_SENSOR_IS_MAX_TC(0)
  #define MAX31865_SENSOR_OHMS_0      100 // (Ω) Typically 100 or 1000 (PT100 or PT1000)
  #define MAX31865_CALIBRATION_OHMS_0 430 // (Ω) Typically 430 for Adafruit PT100; 4300 for Adafruit PT1000
#endif
#if TEMP_SENSOR_IS_MAX_TC(1)
  #define MAX31865_SENSOR_OHMS_1      100
  #define MAX31865_CALIBRATION_OHMS_1 430
#endif
#if TEMP_SENSOR_IS_MAX_TC(2)
  #define MAX31865_SENSOR_OHMS_2      100
  #define MAX31865_CALIBRATION_OHMS_2 430
#endif
#if HAS_E_TEMP_SENSOR
  #define TEMP_RESIDENCY_TIME         10  // (seconds) Time to wait for hotend to "settle" in M109
  #define TEMP_WINDOW                  1  // (°C) Temperature proximity for the "temperature reached" timer
  #define TEMP_HYSTERESIS              3  // (°C) Temperature proximity considered "close enough" to the target
#endif
#if TEMP_SENSOR_BED
  #define TEMP_BED_RESIDENCY_TIME     10  // (seconds) Time to wait for bed to "settle" in M190
  #define TEMP_BED_WINDOW              1  // (°C) Temperature proximity for the "temperature reached" timer
  #define TEMP_BED_HYSTERESIS          3  // (°C) Temperature proximity considered "close enough" to the target
#endif
#if TEMP_SENSOR_CHAMBER
  #define TEMP_CHAMBER_RESIDENCY_TIME 10  // (seconds) Time to wait for chamber to "settle" in M191
  #define TEMP_CHAMBER_WINDOW          1  // (°C) Temperature proximity for the "temperature reached" timer
  #define TEMP_CHAMBER_HYSTERESIS      3  // (°C) Temperature proximity considered "close enough" to the target
#endif
#if TEMP_SENSOR_REDUNDANT
  #define TEMP_SENSOR_REDUNDANT_SOURCE    E1  // The sensor that will provide the redundant reading.
  #define TEMP_SENSOR_REDUNDANT_TARGET    E0  // The sensor that we are providing a redundant reading for.
  #define TEMP_SENSOR_REDUNDANT_MAX_DIFF  10  // (°C) Temperature difference that will trigger a print abort.
#endif
#define HEATER_0_MINTEMP   5
#define HEATER_1_MINTEMP   5
#define HEATER_2_MINTEMP   5
#define HEATER_3_MINTEMP   5
#define HEATER_4_MINTEMP   5
#define HEATER_5_MINTEMP   5
#define HEATER_6_MINTEMP   5
#define HEATER_7_MINTEMP   5
#define BED_MINTEMP        5
#define CHAMBER_MINTEMP    5
#define HEATER_0_MAXTEMP 275
#define HEATER_1_MAXTEMP 275
#define HEATER_2_MAXTEMP 275
#define HEATER_3_MAXTEMP 275
#define HEATER_4_MAXTEMP 275
#define HEATER_5_MAXTEMP 275
#define HEATER_6_MAXTEMP 275
#define HEATER_7_MAXTEMP 275
#define BED_MAXTEMP      150
#define CHAMBER_MAXTEMP  60
#define HOTEND_OVERSHOOT 15   // (°C) Forbid temperatures over MAXTEMP - OVERSHOOT
#define BED_OVERSHOOT    10   // (°C) Forbid temperatures over MAXTEMP - OVERSHOOT
#define COOLER_OVERSHOOT  2   // (°C) Forbid temperatures closer than OVERSHOOT
#define PIDTEMP           // See the PID Tuning Guide at https://reprap.org/wiki/PID_Tuning
#define PID_MAX  255      // Limit hotend current while PID is active (see PID_FUNCTIONAL_RANGE below); 255=full current
#define PID_K1     0.95   // Smoothing factor within any PID loop
    #define DEFAULT_Kp  22.20
    #define DEFAULT_Ki   1.08
    #define DEFAULT_Kd 114.00
#define MAX_BED_POWER 255 // limits duty cycle to bed; 255=full current
#define MAX_CHAMBER_POWER 255 // limits duty cycle to chamber heater; 255=full current
  #define PID_FUNCTIONAL_RANGE 10 // If the temperature difference between the target temperature and the actual temperature
#define PREVENT_COLD_EXTRUSION
#define EXTRUDE_MINTEMP 170
#define PREVENT_LENGTHY_EXTRUDE
#define EXTRUDE_MAXLENGTH 200
#define THERMAL_PROTECTION_HOTENDS // Enable thermal protection for all extruders
#define THERMAL_PROTECTION_BED     // Enable thermal protection for the heated bed
#define THERMAL_PROTECTION_CHAMBER // Enable thermal protection for the heated chamber
#define THERMAL_PROTECTION_COOLER  // Enable thermal protection for the laser cooling
#define USE_ZMIN_PLUG
#define USE_XMAX_PLUG
#define USE_YMAX_PLUG
#define ENDSTOPPULLUPS
#define X_MIN_ENDSTOP_INVERTING false // Set to true to invert the logic of the endstop.
#define Y_MIN_ENDSTOP_INVERTING false // Set to true to invert the logic of the endstop.
#define Z_MIN_ENDSTOP_INVERTING true // Set to true to invert the logic of the endstop.
#define I_MIN_ENDSTOP_INVERTING false // Set to true to invert the logic of the endstop.
#define J_MIN_ENDSTOP_INVERTING false // Set to true to invert the logic of the endstop.
#define K_MIN_ENDSTOP_INVERTING false // Set to true to invert the logic of the endstop.
#define U_MIN_ENDSTOP_INVERTING false // Set to true to invert the logic of the endstop.
#define V_MIN_ENDSTOP_INVERTING false // Set to true to invert the logic of the endstop.
#define W_MIN_ENDSTOP_INVERTING false // Set to true to invert the logic of the endstop.
#define X_MAX_ENDSTOP_INVERTING true // Set to true to invert the logic of the endstop.
#define Y_MAX_ENDSTOP_INVERTING true // Set to true to invert the logic of the endstop.
#define Z_MAX_ENDSTOP_INVERTING true // Set to true to invert the logic of the endstop.
#define I_MAX_ENDSTOP_INVERTING false // Set to true to invert the logic of the endstop.
#define J_MAX_ENDSTOP_INVERTING false // Set to true to invert the logic of the endstop.
#define K_MAX_ENDSTOP_INVERTING false // Set to true to invert the logic of the endstop.
#define U_MAX_ENDSTOP_INVERTING false // Set to true to invert the logic of the endstop.
#define V_MAX_ENDSTOP_INVERTING false // Set to true to invert the logic of the endstop.
#define W_MAX_ENDSTOP_INVERTING false // Set to true to invert the logic of the endstop.
#define Z_MIN_PROBE_ENDSTOP_INVERTING false // Set to true to invert the logic of the probe.
#define DEFAULT_AXIS_STEPS_PER_UNIT   { 80, 80, 400, 780 }
#define DEFAULT_MAX_FEEDRATE          { 80, 80, 60, 100 }
#define DEFAULT_MAX_ACCELERATION      { 600, 600, 60, 30000 }
#define DEFAULT_ACCELERATION          3000    // X, Y, Z and E acceleration for printing moves
#define DEFAULT_RETRACT_ACCELERATION  3000    // E acceleration for retracts
#define DEFAULT_TRAVEL_ACCELERATION   3000    // X, Y, Z acceleration for travel (non printing) moves
#define DEFAULT_EJERK    5.0  // May be used by Linear Advance
  #define JUNCTION_DEVIATION_MM 0.013 // (mm) Distance from real junction edge
  #define JD_HANDLE_SMALL_SEGMENTS    // Use curvature estimation instead of just the junction angle
#define Z_MIN_PROBE_USES_Z_MIN_ENDSTOP_PIN
#define PROBE_MANUALLY
#define NOZZLE_TO_PROBE_OFFSET { 10, 10, 0 }
#define PROBING_MARGIN 10
#define XY_PROBE_FEEDRATE (133*60)
#define Z_PROBE_FEEDRATE_FAST (4*60)
#define Z_PROBE_FEEDRATE_SLOW (Z_PROBE_FEEDRATE_FAST / 2)
#define Z_CLEARANCE_DEPLOY_PROBE   10 // (mm) Z Clearance for Deploy/Stow
#define Z_CLEARANCE_BETWEEN_PROBES  5 // (mm) Z Clearance between probe points
#define Z_CLEARANCE_MULTI_PROBE     5 // (mm) Z Clearance between multiple probes
#define Z_PROBE_LOW_POINT          -2 // (mm) Farthest distance below the trigger-point to go before stopping
#define Z_PROBE_OFFSET_RANGE_MIN -20
#define Z_PROBE_OFFSET_RANGE_MAX 20
#define X_ENABLE_ON 0
#define Y_ENABLE_ON 0
#define Z_ENABLE_ON 0
#define E_ENABLE_ON 0 // For all extruders
#define DISABLE_OTHER_EXTRUDERS   // Keep only the active extruder enabled
#define INVERT_X_DIR false
#define INVERT_Y_DIR false
#define INVERT_Z_DIR false
#define INVERT_E0_DIR false
#define INVERT_E1_DIR false
#define INVERT_E2_DIR false
#define INVERT_E3_DIR false
#define INVERT_E4_DIR false
#define INVERT_E5_DIR false
#define INVERT_E6_DIR false
#define INVERT_E7_DIR false
#define X_HOME_DIR 1
#define Y_HOME_DIR 1
#define Z_HOME_DIR -1
#define X_BED_SIZE 280
#define Y_BED_SIZE 220
#define X_MIN_POS 0
#define Y_MIN_POS 0
#define Z_MIN_POS 0
#define X_MAX_POS X_BED_SIZE
#define Y_MAX_POS Y_BED_SIZE
#define Z_MAX_POS 300
#define MIN_SOFTWARE_ENDSTOPS
  #define MIN_SOFTWARE_ENDSTOP_X
  #define MIN_SOFTWARE_ENDSTOP_Y
  #define MIN_SOFTWARE_ENDSTOP_Z
  #define MIN_SOFTWARE_ENDSTOP_I
  #define MIN_SOFTWARE_ENDSTOP_J
  #define MIN_SOFTWARE_ENDSTOP_K
  #define MIN_SOFTWARE_ENDSTOP_U
  #define MIN_SOFTWARE_ENDSTOP_V
  #define MIN_SOFTWARE_ENDSTOP_W
#define MAX_SOFTWARE_ENDSTOPS
  #define MAX_SOFTWARE_ENDSTOP_X
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

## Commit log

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2025-04-30 Create t extrusion model
    [2020_t_extrusion.FCStd]
2025-04-30 Added missing fillet
    [2020_t_extrusion.FCStd]
2025-04-30 Create v extrusion model
    [2020_v_extrusion.FCStd]
2025-04-30 Create linear slider model
    [2020_t_extrusion.FCStd, 2020_v_extrusion.FCStd, linear_slider.FCStd]
2025-05-02 Added Aluminum plate and linear bearing models
    [0_aluminum_plate.FCStd, 1_linear_bearing.FCStd, BOM.csv]
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2025-05-02 Modelled belt clamp and added to y-axis
    [0_aluminum_plate.FCStd, 1_linear_bearing.FCStd, 2_belt_clamp.FCStd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]
2025-05-02 Update bed size and bearing type
    [0_aluminum_plate.FCStd, 1_linear_bearing.FCStd, 2_belt_clamp.FCStd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]
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2025-05-02 Fixed assembly
    [0_aluminum_plate.FCStd, y_axis_assembly.FCStd]
2025-05-02 Added end caps, broke up assembly (freecad is struggling)
    [4_rod_end_caps.FCStd, y_axis_assembly.FCStd, y_axis_plate.FCStd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]
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2025-05-02 Added 10mm placeholder gap on y-axxis plate
    [y_axis_assembly.FCStd, y_axis_plate.FCStd]
2025-05-03 Moddeled spacer for y-axis bearings
    [bearing_spacers_y_axis.FCStd, y_axis_frame.FCStd]
2025-05-04 Rebuilt assemblies with spacers to raise plate
    [y_axis_assembly.FCStd, y_axis_bearings.FCStd, y_axis_plate.FCStd]
2025-05-04 Created Y-axis frame and added to assembly
    [2020_t_extrusion.FCStd, 5_2020_t_extrusion_400mm.FCStd, 6_2020_t_extrusion_300mm.FCStd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]
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2025-05-04 Created stepper sub_assembly and added it to Y-axis
    [stepper_motor.FCStd, timing_pulley_wheel.FCStd, y_axis_assembly.FCStd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]
2025-05-04 Repositioned motor in assembly, Belt clip will need to be moved to keep motor from interfering with linear bearings
    [y_axis_assembly.FCStd]
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2025-05-07 Idler for timing belts
    [8_timing_idler.FCStd, full_frame.FCStd]
2025-05-07 Readme updates and started modeling hotend
    [heat_break.FCStd, nozzle.FCStd]
2025-05-07 Readme and assembly updates
    [0_aluminum_plate.FCStd, 4_1_rod_end_caps_offset.FCStd, full_build.FCStd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]
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2025-05-09 Updating offset rod end
    [4_1_rod_end_caps_offset.FCStd, full_build.FCStd]
2025-05-09 Started work on z-axis assembly and updated images in readme
    [10_stepper_bracket.FCStd, 11_stepper_motor.FCStd, 12_timing_pulley_wheel.FCStd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]
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2025-05-11 Created lead screw flange models and updated images
    [15_1_lead_screw_flange.FCStd, 15_2_lead_screw_flange.FCStd, 15_3_lead_screw_flange.FCStd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]
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2025-05-12 Add linear bearings to z axis
    [full_build.FCStd, z_axis_assembly.FCStd]
2025-05-14 Tweaked z-axis to align rails and lead screws
    [14_lead_screw_top_bracket.FCStd, full_build.FCStd, z_axis_assembly.FCStd]
2025-05-14 Basic X-Axis build and readme updates
    [16_1_xz_bracket_motor.FCStd, 16_xz_bracket.FCStd, 3_1_linear_rod_400.FCStd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]
2025-05-27 Update BOM for MK0
    [BOM.csv, MK0_BOM.csv]
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2025-06-25 First pass on Marlin config
    [Configuration.h]
2025-06-25 Switched to stable Marlin release
    [Configuration.h, Configuration_adv.h]
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2025-06-25 Firmware compiles, LCD blank on power up
    [Configuration.h]
2025-06-25 Fixed LCD
    [Configuration.h]
2025-06-25 Fixed some bugs and turned down feedrate temporarily for belt axis
    [Configuration.h]
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2025-06-30 Fix endstop config (I hope)
    [Configuration.h]
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2025-07-01 Made a lil cube
    [Configuration.h, cube_10mm-Body.stl, cube_10mm.FCStd]
2025-07-02 Disable speaker, will reenable once everything is working correctly
    [Configuration.h]
2025-07-02 Undoing most recent change (pin conflict) will desolder buzzer
    [Configuration.h]
2025-07-03 Reduce max feedrate and acceleration until things are more stable
    [Configuration.h]
2025-07-12 Moved z endstop to bottom
    [Configuration.h]
2025-07-13 Tweak config and add 40mm cube
    [Configuration.h, cube_40mm-Body.stl, cube_40mm.FCStd]
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2025-07-16 Update readme and add new MK0 docs
    [MK0_BOM.csv]
2025-07-18 Added folder and file for custom parts
    [Configuration.h, cura_slicer_settings.3mf]
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2025-07-23 Created sleeve part to tighten bed slop
    [bed_leveling_sleeve.stl]
2025-08-06 Increase tolerances on sleeve
    [bed_leveling_sleeve.stl]
2025-08-08 Created basic xy_endstop bracket
    [xy_endstop_bracket.stl]
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2025-08-15 Reverse holes on endstop bracket
    [xy_endstop_bracket.stl]
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2025-08-15 Made rough frame reenforcement bracket
    [z_frame_reenforcement_bracket.stl]
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2025-08-22 First pass of a foot, needs some refinement
    [feet.stl]
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2025-10-01 Create model for press fits
    [press_fit_test1.FCStd, press_fit_test1.stl]
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2025-10-01 updated hole placement on z_top_bracket
    [z_top_bracket.stl]
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2025-10-03 z_bottom_bracket update sleeve for linear rod
    [z_bottom_bracket.stl]
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2025-10-04 spacer for z top_bracket
    [z_top_bearing_spacer.stl]
2025-10-04 Made a test plate to help withe geometry of print head
    [test_plate.stl]
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2025-10-06 Updated test plate to refine measurements
    [test_plate.stl]
2025-10-08 Test plate take 3
    [test_plate.stl]
2025-10-08 Working on z_carriage (Print head attachment))
    [test_plate.stl]
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2025-10-22 Start creating documentation for MK1
    [MK1_BOM.csv]
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2025-10-24 created rod test stl to check fit of z carriage on threaded axle
    [z_carriage_rod_test.stl]
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2025-11-28 Doc updates and new images
    [spool_holder_main.stl]
2025-11-28 Deleted x and z assemblies to rebuild with updated parts
    [x_axis_rail.FCStd, x_axis_rails_and_brackets.FCStd, x_axis_xz_bracket.FCStd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]
2025-12-02 Spool holder reworks
    [spool_holder_base.stl, spool_holder_main.stl, spool_holder_post.stl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]
2025-12-29 Y_bracket first pass and other updates
    [spool_holder_clip.stl, spool_holder_clip_narrow.stl, spool_holder_post.stl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]
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2025-12-31 Test plates for electrical box
    [test_plate_arduino_mega.stl, test_plate_reprap_screen.stl]
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2026-01-06 First pass of electronics box for fit checks
    [electronics_box_front.stl, electronics_box_main.stl, electronics_box_top.stl]
2026-01-06 fw tweaks to try to fix mirroring issue
    [Configuration.h]
2026-01-06 simple model to test axis mirroring bug
    [axis_test_arrow.FCStd, axis_test_arrow.stl]
2026-01-07 fw fix for mirroring
    [Configuration.h]
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2026-01-09 adjusted z reenforcement size to make room for endstop
    [z_endstop_bracket.stl, z_frame_reenforcement_bracket_v2.stl]
2026-01-10 Created electrical diagram for connectors
    [connectors.kicad_pcb, connectors.kicad_sch]
2026-01-10 Added connector diagram to readme
    [connectors.kicad_sch]
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

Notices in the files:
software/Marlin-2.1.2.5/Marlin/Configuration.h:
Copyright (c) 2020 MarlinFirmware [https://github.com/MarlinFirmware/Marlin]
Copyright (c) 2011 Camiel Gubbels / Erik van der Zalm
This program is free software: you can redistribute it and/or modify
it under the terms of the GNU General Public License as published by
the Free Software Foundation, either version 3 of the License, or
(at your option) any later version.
